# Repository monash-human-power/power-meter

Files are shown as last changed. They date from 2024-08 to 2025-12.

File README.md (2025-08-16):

# Cycling power meter final year project <!-- omit in toc -->
Oscar Varney and Jotham Gates, 2024

This is the code repository for a Final Year Project (FYP) to develop a crankset and power meter for Human Powered Vehicles (HPVs).

<p align="center">
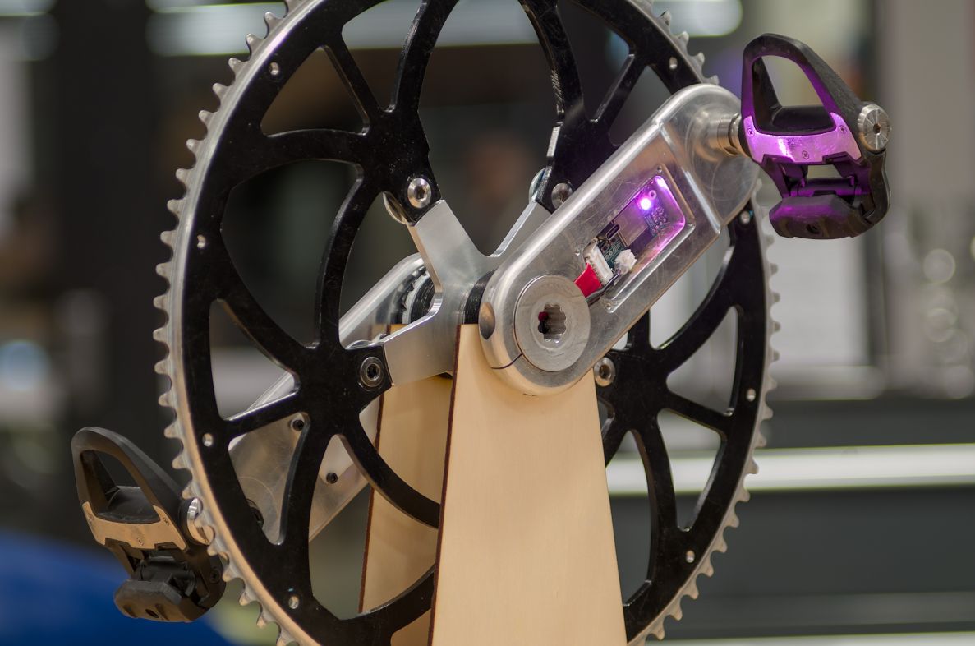
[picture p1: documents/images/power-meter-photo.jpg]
Pretty photo of the prototype crankset and power meter
    
</p>

## Contents <!-- omit in toc -->
- [Getting started](#getting-started)
- [Schematic and PCB layout](#schematic-and-pcb-layout)
- [Code](#code)
  - [Libraries](#libraries)
  - [Tools for updating dates of changed files and versions](#tools-for-updating-dates-of-changed-files-and-versions)
    - [Git Hook for checking dates are correct before committing](#git-hook-for-checking-dates-are-correct-before-committing)
  - [Doxygen documentation](#doxygen-documentation)
- [Scripts and testing](#scripts-and-testing)

## Getting started
- See [here](./documents/getting_started_mqtt.md) for some instructions on getting the power meter to work with MQTT and WiFi.
- See [here](./configs/README.md) for information on configuring the power meter.
- See [here](./documents/mqtt_topics.md) for information on MQTT topics used when communicating using this protocol.
- If you are a member of MHP, then the Notion page for this project can be found [here](https://www.notion.so/monashhumanpower/Power-Pedals-Cranks-FYP-3e6eb409a05642b1ad961b32c2f40aa7).
- The reports submitted for the project are [here](https://github.com/monash-human-power/power-meter-docs/releases) (private repository).

## Schematic and PCB layout
The schematic and PCB layout were completed using [KiCAD 9](https://www.kicad.org/). The design files are in the [`power-meter-pcb`](./power-meter-pcb/) folder.

## Code
The firmware is written to use the Arduino environment of Platform IO and is located in the [`power-meter-code`](power-meter-code) directory.

### Libraries
Install the following libraries, either by using the Arduino library manager or going to their GitHub repository and cloning them.
- [ArduinoJson](https://arduinojson.org/) library for JSON encoding and decoding.
- [ICM42670P](https://github.com/tdk-invn-oss/motion.arduino.ICM42670P) library for communicating with the IMU.
- [BasicLinearAlgebra](https://github.com/tomstewart89/BasicLinearAlgebra/) library for matrix maths. This is also added as a submodule for testing the Kalman filter on a computer.
- [ArduinoBLE](https://github.com/arduino-libraries/ArduinoBLE) library for Bluetooth Low Energy (BLE) communications.
- [PubSubClient](https://pubsubclient.knolleary.net/) library for communicating using MQTT over WiFi.

### Tools for updating dates of changed files and versions
A bash script has been written to update the dates on all modified or staged files (not including untracked files). To perform this operation, run:
```bash
./tools/update_date.sh
```

Another script is included to update the version info on all files and definitions for the code. The files and elements updated include:
- Any `@version` tags in the code directory.
- The `VERSION` definition in [`defines.h`](./power-meter-code/defines.h).
- The Doxygen version number in [`Doxyfile`](./Doxyfile).

As an example:
```bash
./tools/update_version.sh 1.2.3
```

#### Git Hook for checking dates are correct before committing
> This needs to be modified to work with the platform IO structure.
Copy the [`pre-commit`](./tools/pre-commit) file into [`.git/hooks/pre-commit`](.git/hooks/pre-commit). This will check the date of code files and make sure they are up to date.

### Doxygen documentation
Documentation can be automatically generated using Doxygen by running `doxygen` from the root folder of the repository. You might need to install doxygen and graphviz first. The output will be placed in the [`docs`](docs) folder. GitHub actions may be set up later down the track to automatically generate and deploy to GitHub pages on commit- however that would require a public repository and documentation.

To generate a massive appendix for the report, run `./tools/generate_refman.sh`

The output file will be [`refman.pdf`](docs/latex/refman.pdf).

## Scripts and testing
Scripts for testing the board hardware and easing development of certain sections can be found in the [`scripts-testing`](./scripts-testing/) directory. This includes python scripts used to log data over MQTT and plot it.

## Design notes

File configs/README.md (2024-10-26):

# Config files <!-- omit in toc -->
These JSON files contain calibration data and settings for the power meters.

- [Config format](#config-format)
  - [Example](#example)
  - [Key value pairs](#key-value-pairs)
  - [Notes](#notes)
    - [(1) More on Kalman filters](#1-more-on-kalman-filters)
    - [(2) Matrix representation](#2-matrix-representation)
    - [(3) Converting ADC values to torque](#3-converting-adc-values-to-torque)
- [Obtaining the current config from the device](#obtaining-the-current-config-from-the-device)
  - [Over MQTT](#over-mqtt)
  - [Through serial](#through-serial)
- [Uploading new configs to the device](#uploading-new-configs-to-the-device)
  - [Uploading over MQTT](#uploading-over-mqtt)
  - [Uploading over serial](#uploading-over-serial)

## Config format
The data is formatted into key-value pairs using JSON.

### Example
```json
{
    "connection": 0,
    "kalman": {
        "Q": [
            [2e-3, 0],
            [0, 0.1]
        ],
        "R": [
            [100, 0],
            [0, 1e-2]
        ]
    },
    "imuHowOften": 1,
    "sleep-time": 0,
    "left-strain": {
        "offset": 0,
        "coef": -3.679656e-4,
        "temp-test": 24.25,
        "temp-coef": 0
    },
    "right-strain": {
        "offset": 0,
        "coef": 2.246571e-4,
        "temp-test": 24.25,
        "temp-coef": 0
    },
    "mqtt": {
        "length": 20,
        "broker": "mhp-chase-car.local"
    },
    "wifi": {
        "ssid": "",
        "psk": "",
        "redacted": true
    }
}
```

### Key value pairs
| Key | Data type | Description | When changes are applied |
| :---: | :---: | :--- | :--- |
| `"connection"` | [`EnumSide`](../power-meter-code/src/defines.h#EnumSide)  | What connection method to use. `0` is MQTT and WiFi, `1` is Bluetooth Low Energy (BLE). Pressing the boot button after the power meter has started will also toggle this option and restart the power meter to apply it. | On boot |
| `"kalman"` | JSON object | Configurration values for the Kalman filter used to process data from the IMU. See [(1)](#1-more-on-kalman-filters) for more info. | |
| `"kalman"` - `"Q"` | $2 \times 2$ matrix (see [(2)](#2-matrix-representation)) | The covariance matrix representing environmental uncertainty. This increases the uncertainty of the historical predictions over time. Without going into details, increasing the top left number will make the system more uncertain about the previously predicted position, whilst increasing the bottom right number will make it more uncertain about the previously predicted velocity. | Instantly |
| `"kalman"` - `"R"` | $2 \times 2$ matrix (see [(2)](#2-matrix-representation)) | The covariance matrix representing measurement uncertainty. This represents the uncertainty of the most recent measurements from the IMU, making the filter rely more on predictions based off historical data. Without going into details, increasing the top left number will make the system more uncertain about the position measured by the accelerometer, whilst increasing the bottom right number will make it more uncertain about the measured velocity. | Instantly |
| `"imuHowOften"` | Integer | How often to save and transmit data from the IMU. `1` is every time. | Instantly |
| `"sleep-time"` | Integer | The number of seconds after the last forwards rotation occurred to go into sleep mode to save power. Setting this to 0 disables sleep mode entirely. For safety reasons / reducing the pain to unbrick if set to too short a value, this value will not be updated if it is between 0 and 20 seconds (inclusive). | Instantly |
| `"left-strain"` `"right-strain"` | JSON object | Calibration data for the strain gauges on each side. See [(3)](#3-converting-adc-values-to-torque) for more information on how these values are used to calculate torque. | |
| `"*-strain"` - `"offset"` | Unsigned 24 bit integer | Reading from the ADC when there is no torque applied. This is the 0 value. | Instantly |
| `"*-strain"` - `"coef"` | float | This is the coeficient used to scale the ADC reading to obtain the torque in Nm from the raw ADC reading. It needs to have the correct sign depending on the wheatstone bridge wiring and side of the meter. | Instantly |
| `"*-strain"` - `"temp-test"` | float | The temperature at which calibration occurred on that side. |
| `"*-strain"` - `"temp-coef"` | float | The temperature coefficient. | Instantly |

### Notes
#### (1) More on Kalman filters
[This](https://www.bzarg.com/p/how-a-kalman-filter-works-in-pictures/) is a really useful website that nicely describes with pictures how a multidimensional Kalman filter works and can be implemented.

The main aims / reasoning of using a Kalman filter are:
- The accelerometer's angle / measurement of the direction of gravity is stable over long periods of time. It is unreliable over short periods due to factors like rocks, vibration and falling off a cliff.
- The gyroscope is highly accurate at measuring instantaneous angular velocity. Finding position from this requires integration, which accrues error and drift over time.
- The filter combines the short term accuracy of the gyroscope with long term stability of the accelerometer to produce a nice, relatively noise free output of angular position and angular velocity.
- 
#### (2) Matrix representation
$2 \times 2$ matrices like the one shown below are represented using 2 dimensional arrays (same way as in numpy).
$$
A = \left[\begin{matrix} a & b \\ c & d\end{matrix}\right]
$$
Will be translated to:
```json
{
    "A": [[a, b], [c, d]]
}
```

#### (3) Converting ADC values to torque
The current formula is:

$$
\tau (x, t) = S_c \times (x - S_o) \times (1 - T_c) \times (t - T_o)
$$

##### Where <!-- omit in toc -->
- $\tau(x, t)$ is the calculated torque, $\tau$ for a given ADC reading, $x$ and temperature in Celcius, $t$.
- $S_c$ is the coefficient for the strain gauges and ADC (`"coef"`).
- $S_o$ is the offset (what the ADC resports when no torque is applied, `"offset"`).
- $T_c$ is the temperature coefficient (set to 0 to disable temperature compensation, `"temp-coef"`).
- $T_o$ is the temperature offset (temperature that the calibration to measure $S_c$ took place, `"temp-test"`).

## Obtaining the current config from the device
### Over MQTT
The config is published as part of a message on the [`/power/about`](../documents/mqtt_topics.md#about-this-device-powerabout) topic when the power meter connects to the broker.

### Through serial
1. Connect a USB cable and open a serial terminal.
2. Press `g` to print out the current config stored on the device. Make changes as necessary.
3. Typing `h` lists other potentially useful commands.

## Uploading new configs to the device
### Uploading over MQTT
These can be uploaded over MQTT using:
```
mosquitto_pub -t "/power/conf" -f FirstPrototype_130.json
```

### Uploading over serial
They can also be uploaded over the serial port:
1. Connect a USB cable and open a serial terminal.
2. Press `g` to print out the current config stored on the device. Make changes as necessary.
3. Press `s` to set the config. Remove all new lines and paste the json document. Press enter if needed afterwards to apply. There is a 30 second time limit.
4. Confirm that the config is successfully set.

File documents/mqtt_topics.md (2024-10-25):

# MQTT Topics <!-- omit in toc -->
When running in WiFi and MQTT mode, the power meter publishes data to several topics. All topics are prefixed by `/power/` to distinguish data sent to and from the power meter with other traffic on the broker.

- [Published topics](#published-topics)
  - [About this device (`/power/about`)](#about-this-device-powerabout)
    - [Example](#example)
    - [Key value pairs](#key-value-pairs)
  - [Housekeeping data (`/power/housekeeping`)](#housekeeping-data-powerhousekeeping)
    - [Example](#example-1)
    - [Key value pairs](#key-value-pairs-1)
  - [Slow speed data (`/power/power`)](#slow-speed-data-powerpower)
    - [Example](#example-2)
    - [Key value pairs](#key-value-pairs-2)
  - [High speed IMU data (`/power/imu`)](#high-speed-imu-data-powerimu)
    - [Record format](#record-format)
  - [High speed strain gauge data (`/power/fast/left`, `/power/fast/right`)](#high-speed-strain-gauge-data-powerfastleft-powerfastright)
    - [Record format](#record-format-1)
- [Subscribed topics](#subscribed-topics)
  - [Set a new configurration (`/power/conf`)](#set-a-new-configurration-powerconf)
  - [Calculate and apply new offsets on the strain gauge ADCs (`/power/offset`)](#calculate-and-apply-new-offsets-on-the-strain-gauge-adcs-poweroffset)
    - [Example usage](#example-usage)
  - [Save configs (`/power/save`)](#save-configs-powersave)
  - [Reboot (`/power/reboot`)](#reboot-powerreboot)
  - [Enter sleep mode (`/power/sleep`)](#enter-sleep-mode-powersleep)
- [Additional notes](#additional-notes)

## Published topics
These topics contain data from the power meter. Messages sent less frequently are formatted using JSON for easier reading and processing. Messages containing high frequency data (IMU and strain gauges) are packed into bytes.

### About this device (`/power/about`)
This message is sent whenever the power meter connects to the broker. It contains information relating to the software and hardware versions, as well as the current configurrations.

#### Example
An example message after pretty-printing is:
```json
{
    "name": "Power meter prototype",
    "compiled": "Sep 30 2024, 22:38:28",
    "sw_version": "s0.1.0",
    "hw_version": "v1.1.1",
    "connect-time": 7336,
    "calibration": {
        "connection": 0,
        "kalman": {
            "Q": [
                [2e-3, 0],
                [0, 0.1]
            ],
            "R": [
                [100, 0],
                [0, 1e-2]
            ]
        },
        "imuHowOften": 1,
        "sleep-time": 0,
        "left-strain": {
            "offset": 0,
            "coef": -3.679656e-4,
            "temp-test": 24.25,
            "temp-coef": 0
        },
        "right-strain": {
            "offset": 0,
            "coef": 2.246571e-4,
            "temp-test": 24.25,
            "temp-coef": 0
        },
        "mqtt": {
            "length": 20,
            "broker": "mhp-chase-car.local"
        },
        "wifi": {
            "ssid": "",
            "psk": "",
            "redacted": true
        }
    },
    "mac": "XX:XX:XX:XX:XX:XX"
}
```

#### Key value pairs
| Key | Data type | Description |
| :---: | :---: | :--- |
| `"name"` | string | The device name, set in [constants.h](../power-meter-code/src/constants.example.h). |
| `"compiled"` | string | The date and time that the firmware was compiled according to the computer that did the compiling. |
|  `"sw_version"`  | string | The firmware version (set in [defines.h](../power-meter-code/src/defines.h)). |
|  `"hw_version"`  | string | The targeted hardware version, set in [constants.h](../power-meter-code/src/constants.example.h). |
| `"connect-time"` | unsigned 32 bit integer | The number of microseconds since the microcontroller was reset. This rills over approximately every hour. |
| `"calibration"`  | JSON object | The current config value loaded into memory. See the [`/power/conf`](#set-a-new-configurration-powerconf) topic or [this page](../configs/README.md) for more details. |
| `"mac"` | string | The MAC address of the microcontroller in the power meter. This is aking to a serial number and is useful for identifying which power meter recorded the data. |

### Housekeeping data (`/power/housekeeping`)
This message is sent once every few seconds and contains information on the device health and environmental conditions. It is designed for information that updates faster than that sent in the [about message](#about-this-device-powerabout), but is not time critical like that sent in the power and high frequency messages.

#### Example
An example message after pretty-printing is:
```json
{
    "temps": {
        "left": 24.00,
        "right": -1000.00,
        "imu": 35.00
    },
    "battery": 3299.00,
    "left-offset": 9848390,
    "right-offset": 6252516
}
```

#### Key value pairs
| Key | Data type | Description |
| :---: | :---: | :--- |
| `"temps"` | JSON object | This field contains the temperatures for each side and that reported by the IMU. All values within this are floating point in Celcius. A value of `-1000.00` represents not being able to successfully communicate with the sensor. |
| `"battery"` | float | The battery voltage in mV. |
| `"left-offset"`, `"right-offset"` | unsigned 32 bit integer | The current offsets being used by each ADC. This value represents 0 torque on each side. |

### Slow speed data (`/power/power`)
This message contains information averaged over the last complete rotation. This message is sent every rotation or every few seconds, whichever comes sooner. Most of the useful data that the riders care about mid-ride will come from this message.

#### Example
An example message after pretty-printing is:
```json
{
    "timestamp": 311280713,
    "cadence": 70.1,
    "rotations": 185,
    "power": 390.6,
    "balance": 50.8
}
```

#### Key value pairs
| Key | Data type | Description |
| :---: | :---: | :--- |
| `"timestamp"` | unsigned 32 bit integer | The system time in microseconds when the last rotation occurred. |
|  `"cadence"`  | float | The average cadence over the last complete rotation in RPM. |
| `"rotations"` | unsigned 32 bit integer | The total number of rotations since the device was reset. |
| `"power"` | float | The power over the last rotation in W. If this message is being sent according to a schedule rather than a rotation completing, this will be 0. |
|  `"balance"`  | float | The pedal balance in percent. A value of 50% means that both sides are recording equal power. A value of 0% means that all power is being generated by one side and a value of 100% means all power is being generated by the other side. TODO: Work out which side is which. |

### High speed IMU data (`/power/imu`)
This message contains multiple records of the 100Hz sampled IMU data. Because a lot of this data needs to be sent over the network, structures of bytes are used rather than converting to ASCII and JSON formats.

Each message is comprised of many individual records. The oldest records are arranged at the start of the message, whilst the most recent are at the back. Each message will be a multiple of the size of each record's length. The number of records per message is set in the [configurration](../configs/README.md).
| Byte offset in record |        Data type        | Size in bytes | 

#### Record format
| Byte offset in record | Data type | Size in bytes | Description |
| :---: | :---: | :---: | :--- |
| 0 | unsigned 32 bit integer | 4 | The device time in microseconds when the sample was captured. |
| 4 | float | 4 | The angular velocity in radians per second of the power meter. This is an output from the on-board Kalman filter. |
| 8 | float | 4 | The position in radians of the power meter. This is an output from the on-board Kalman filter. |
| 12 | float | 4 | The acceleration in m/s^2 for the X axis. This has been corrected for centripedal forces caused by the IMU not being at the center of rotation of the power meter. |
| 16 | float | 4 | The acceleration in m/s^2 for the Y axis. This has been corrected for centripedal forces caused by the IMU not being at the center of rotation of the power meter. |
| 20 | float | 4 | The acceleration in m/s^2 for the Z axis. |
| 24 | float | 4 | The angular velocity of the X axis in radians per second as measured by the gyroscope. |
| 28 | float | 4 | The angular velocity of the Y axis in radians per second as measured by the gyroscope. |
| 32 | float | 4 | The angular velocity of the Z axis in radians per second as measured by the gyroscope. |

### High speed strain gauge data (`/power/fast/left`, `/power/fast/right`)
This message contains multiple records of the 80Hz sampled strain gauge data for a side. Because a lot of this data needs to be sent over the network, structures of bytes are used rather than converting to ASCII and JSON formats.

Each message is comprised of many individual records. The oldest records are arranged at the start of the message, whilst the most recent are at the back. Each message will be a multiple of the size of each record's length. The number of records per message is set in the [configurration](../configs/README.md).

#### Record format
| Byte offset in record | Data type | Size in bytes | Description |
| :---: | :---: | :---: | :--- |
| 0 | unsigned 32 bit integer | 4 | The device time in microseconds when the sample was captured. |
| 4 | float | 4 | The angular velocity in radians per second of the power meter. This is an output from the on-board Kalman filter that has been predicted at the current time. |
| 8 | float | 4 | The position in radians of the power meter. This is an output from the on-board Kalman filter that has been predicted at the current time. |
| 12 | unsigned 24 bit integer | 4 | The raw reading from the ADC. Whilst the output from the ADCs is a 24 bit number, the value is being sent as an unsigned 32 bit integer to simplify processing. |
| 16 | float | 4 | The calculated torque in Nm. |
| 20 | float | 4 | The calculate power in W. This is the torque multiplied by the angular velocity. |
| 24 | bool | 1 | Whether the device was transmitting when the sample was taken. This might be useful for noise filtering as the power supply on the microcontroller side is affected. |

## Subscribed topics
### Set a new configurration (`/power/conf`)
See [here](../configs/README.md) for more information on the message format and alternative ways to set configs.

### Calculate and apply new offsets on the strain gauge ADCs (`/power/offset`)
Messages sent to this topic will cause the device to take many samples from the ADC, average them and use them as the offset from now on. These offsets are not stored in flash memory and will be restored to the defaults or those loaded into flash memory upon reboot.

#### Example usage
```bash
mosquitto_pub -t "/power/offset" -m ""
```

### Save configs (`/power/save`)
*Not implemented yet.*

### Reboot (`/power/reboot`)
This would be useful to load new configs / start from a defined base.
*Not implemented yet.*

### Enter sleep mode (`/power/sleep`)
This would be useful to shut the system down and save power manually. It would also be useful to cleanly disconnect from the current connection so that the router / device managing the connection doesn't throw a wobbly if power is removed and reapplied with no warning.

*Not implemented yet.*

## Additional notes
- Integers are sent using little endian.
- Floats are single precision for improved processing performance. They are stored and sent in the IEEE 754 binary32 format (native on the ESP32 and most computers).

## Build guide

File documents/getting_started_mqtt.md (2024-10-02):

# Getting started (connecting over WiFi and MQTT) <!-- omit in toc -->

- [What you will need](#what-you-will-need)
- [Setting up to log and display data](#setting-up-to-log-and-display-data)
- [Turning the power meter on](#turning-the-power-meter-on)

## What you will need
- A WiFi network / mobile phone hotspot (2.4GHz) that the power meter is configurred to connect to (see [configurations](../configs/README.md)).
- An MQTT broker that the power meter is configurred to connect to (see [configurations](../configs/README.md)).
- A computer with:
  - A copy of this repository cloned to it.
  - [Python3](https://www.python.org/) installed.
  - The MQTT broker and WiFi network may be running or hosted on this computer (optional).

## Setting up to log and display data
1. Open a terminal and change the working directory to the [repository root](../).
2. **Optional:** Create a python virtual environment to keep the packages installed in this project separate from the rest of the system.
    ```bash
    # Linux
    pip3 -m venv .venv

    # Windows
    pip -m venv venv
    ```
3. Activate the virtual environment if using it.
    ```bash
    # Linux
    source .venv/bin/activate

    # Windows
    # See 
    venv\Scripts\Activate.ps1
    ```
    You will notive that each line in the terminal now starts with `(.venv)`.
4. Install the required packages:
    ```bash
    pip3 install -r requirements.txt
    ```
5. Change directory to the [`scripts-testing/python-clients`](../scripts-testing/python-clients/) folder.
6. Run the [logging script](../scripts-testing/python-clients/log_power_meter.py):
    ```bash
    ./log_power_meter.py
    ```
    By default, this will attempt to subscribe to a broker running on the same computer the script is being run from. Pass `-h HOST_OR_IP` to change this. To see other options available, run the script with `--help`.
7. It may be worthwhile opening another terminal to subscribe to the low speed topics to display messages as they arrive with:
    ```bash
    mosquitto_sub -t "/power/about" -t "/power/power" -t "/power/housekeeping" -v
    ```
    Again use `-h HOST_OR_IP` to specify an alternate MQTT broker if needed.
8. Use `Ctrl` + `C` to close both of these programmes.

## Turning the power meter on
1. Install the battery and plug it into the board. Make sure the end cap on the axle is done up sufficiently to stop the crank arm falling off.
2. The V1.1.1 power meters will flash the yellow LEDs on each side followed by a blue flash on the RGB LED when they are trying to connect to WiFi. Make sure that the yellow LEDs on both sides are flashing (sometimes power needs to be removed and re-applied to get the temperature sensors they are connected to, to initialise correctly).
3. If the power meter is stuck in this connecting to WiFi state, make sure that the WiFi network is running with the same SSID and password as the power meter is configured to connect to. Make sure that it uses 2.4GHz WiFi as the built in microcontroller does not support the 5GHz band. If none of these work, use a [USB cable to check and update the configs on the device as needed](../configs/README.md#through-serial).
4. Once connected to WiFi, the yellow LEDs on each side will continue to flash and the RGB LED will flash green. In this state, the device is trying to connect to the broker. If this does not happen successfully, make sure the broker is configurred correctly and the broker is running and reachable from other computers.
5. The RGB LED will flicker green when the power meter is connected and sending data.
6. To manually measure and apply offsets, publish a message to the `/power/offset` topic using the following command:
    ```bash
    mosquitto_pub -t "/power/offset" -m ""
    ```

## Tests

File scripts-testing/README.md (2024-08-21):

# Testing scripts and development
## Logging data to a file and plotting it.
The python scripts in the [`python-clients`](./python-clients/) directory allow data to be saved, unpacked into human-readable form and saved as needed.
- [`log_power_meter.py`](./python-clients/log_power_meter.py) logs data to a folder of files or displays it live.
- [`plot_imu_timeseries.py`](./python-clients/plot_imu_timeseries.py) plots IMU data.

## Board testing
These scripts help to verify that the hardware is working correctly. It is recommended to run these scripts in the following order. The next one usually depends on the previous working.

### 1. [LED testing](./led-testing/)
This script turns on and flashes the red and green LEDs (D1 and D2).

### 2. [Accelerometer polling](./accel-testing/)
> Relies on [LED testing](#1-led-testing) passing.

This script regularly polls the IMU and sets the colour of the LEDs based on the readings of the X axis accelerometer (tilt to change colour). The values read are also sent over the serial port.

This script is based off the [ICM42670P Arduino library `Polling_SPI`](https://github.com/tdk-invn-oss/motion.arduino.ICM42670P/blob/main/examples/Polling_SPI/Polling_SPI.ino) example.

### 3. [Accelerometer interrupts](./accel_testing-fifo/)
> Relies on [LED testing](#1-led-testing) and [Accelerometer polling](#2-accelerometer-polling) passing.

This script behaves the same as the polling script, however it uses the FIFO buffer and interrupts to obtain the data.

This script is based off the [ICM42670P Arduino library `FIFO_Interrupt`](https://github.com/tdk-invn-oss/motion.arduino.ICM42670P/blob/main/examples/FIFO_Interrupt/FIFO_Interrupt.ino) example.

### 4. [GPIO Testing for the ADC pins](./gpio-testing/)
> Relies on [LED testing](#1-led-testing) and USB / the ability to accept numbers from `Serial.parseInt()`.

This script toggles pins as given over the serial port. This can be used to check that they were soldered correctly and are not disconnected or shorted out.

Usage instructions:
- Red light indicates waiting for a pin number to be typed in the serial console.
- Flashing green indicates that a pin is being tested (on is high, off is low).
- Press 'q' to got back and select another pin.
- All pins other than LEDs are left in high impedance states after testing that pin concludes.

### 5. Temperature sensor and LED testing
> Relies on [LED testing](#1-led-testing) for pretty lights and a serial connection to show temperatures.

This script reads the temperatures on both I2C sensors and flashes the temperature sensor and built in LEDs.

## Kalman filter development
[`kalman-compare.py`](./kalman-filter/kalman-compare.py) takes a CSV file from the power meter and plots the reported orientation over time. This script also calculates orientation based on the accelerometer alone, gyroscope alone and a python implementation of the Kalman filter to compare the results.

The [`AccelGyroData.ipynb`](./kalman-filter/AccelGyroData.ipynb) Jupyter notebook contains initial code used to test the Kalman filter algorithm with data recorded from a phone taped to a bicycle crank prior to the actual hardware being available. The data was recorded using the [Sensor Logger app](https://play.google.com/store/apps/details?id=com.kelvin.sensorapp&hl=en_US).

[`kalman_test.cpp`](./kalman-filter/kalman_test.cpp) tests the actual Kalman filter implementation whilst running on a computer. Compile this programme using `make kalman` and run it using `make run`.

The [BasicLinearAlgebra](https://github.com/tomstewart89/BasicLinearAlgebra/) library is included as a submodule to assist.

## Python libraries and environments
The [`requirements.txt`](../requirements.txt) file in the root of the repository contains all necessary libraries for all python scripts and Jupyter notebooks in this repository. As usual, it is recommended to use a python virtual environment. This can be created and the libraries installed (running from the repository-root directory) using:
```bash
python3 -v venv .venv
source .venv/bin/activate
pip3 -r requirements.txt
```

To save / update [`requirements.txt`](../requirements.txt), run [`./tools/update_requirements.sh`](../tools/update_requirements.sh) or run:
```bash
source .venv/bin/activate
pip3 freeze > requirements.txt
```

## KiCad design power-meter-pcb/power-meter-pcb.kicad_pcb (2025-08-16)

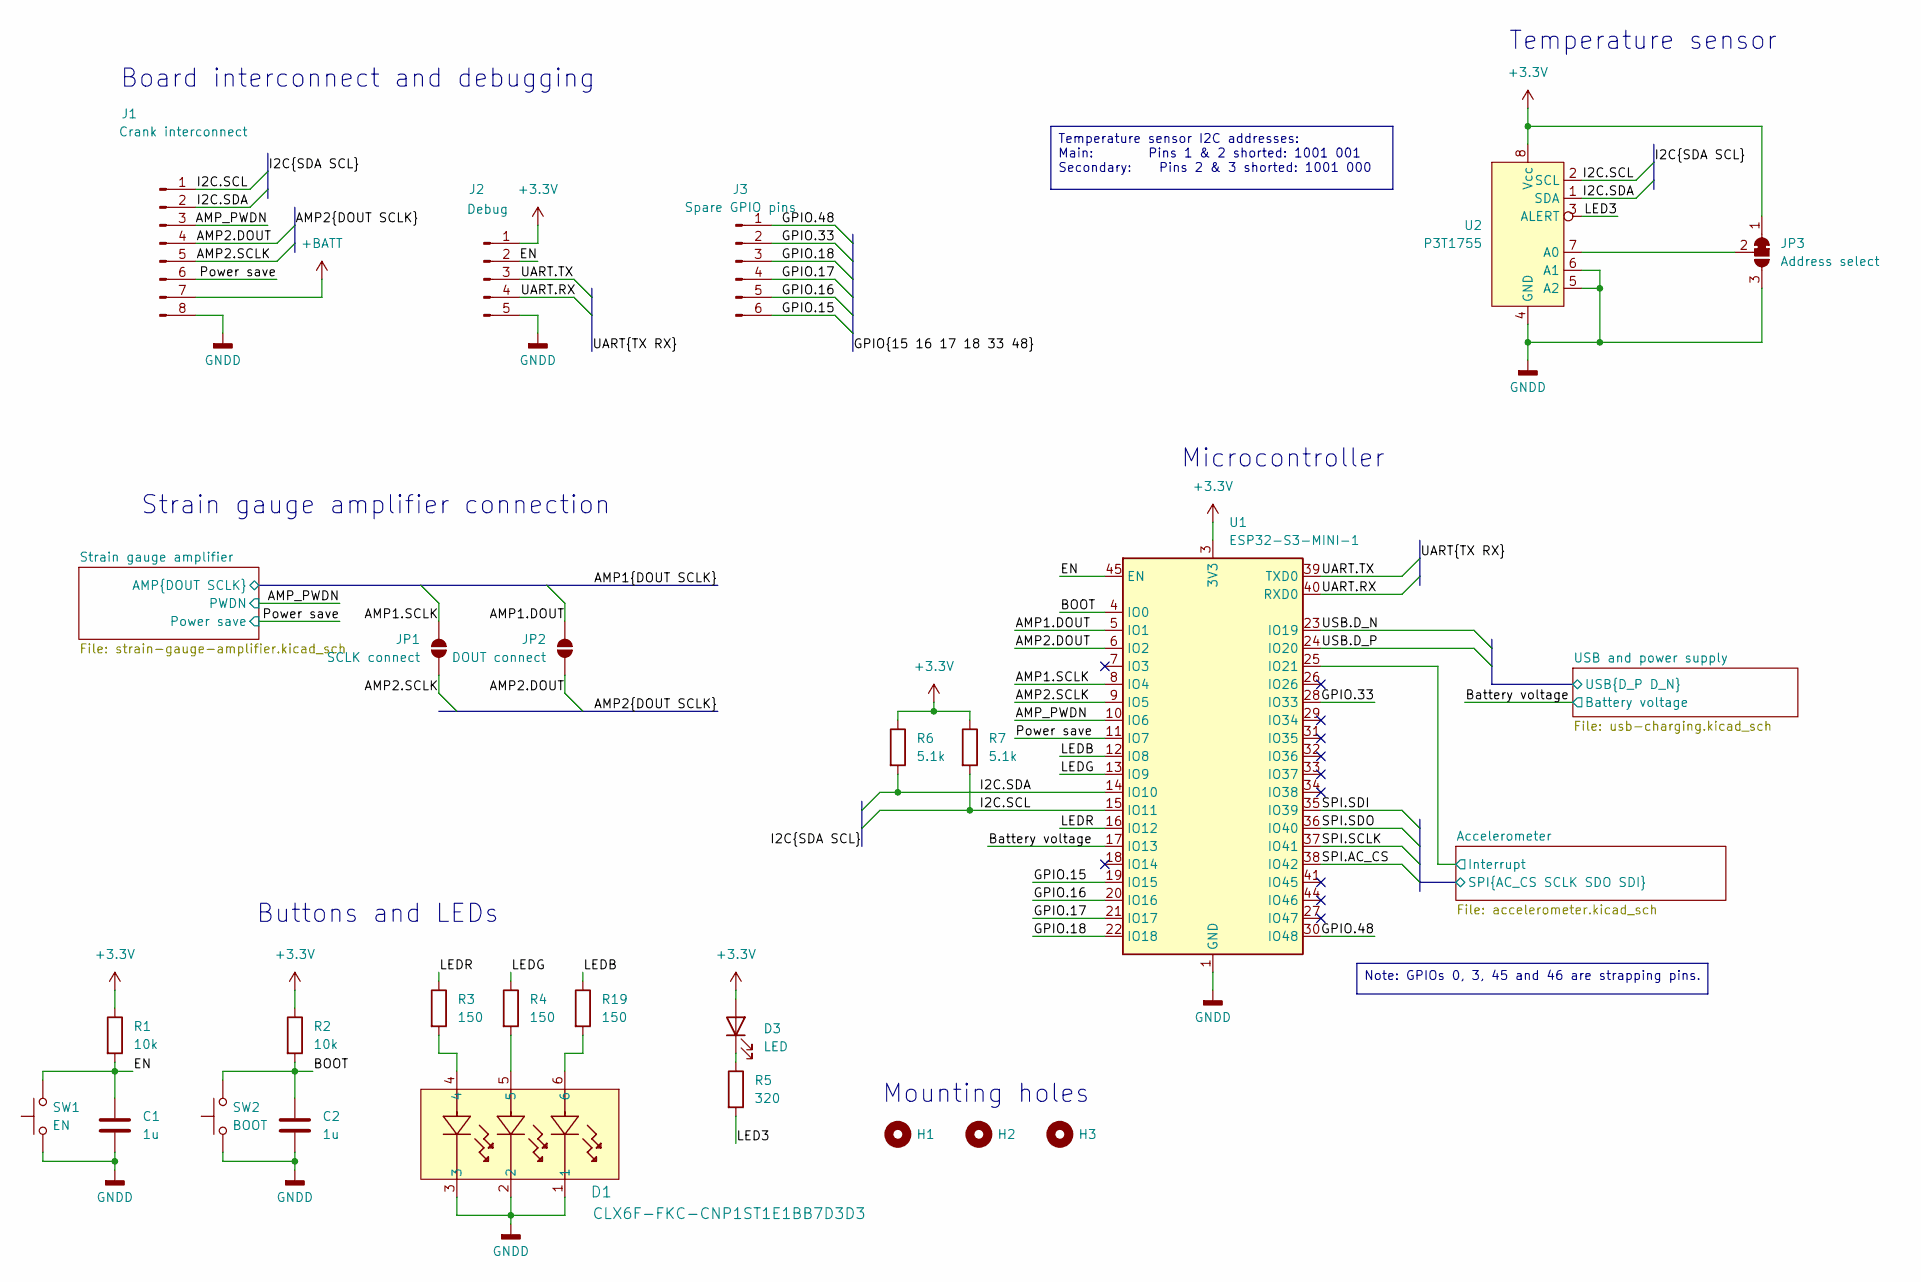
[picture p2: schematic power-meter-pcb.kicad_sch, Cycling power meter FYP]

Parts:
C1, C2: 1u; C_0603_1608Metric_Pad1.08x0.95mm_HandSolder
D1: CLX6F-FKC-CNP1ST1E1BB7D3D3; PLCC6_3.4X3.4_CRW-M
D3: LED; LED_0603_1608Metric_Pad1.05x0.95mm_HandSolder
H1, H2, H3: MountingHole; MountingHole_2.2mm_M2
J1: Crank interconnect; JST_PH_S8B-PH-K_1x08_P2.00mm_Horizontal
J2: Debug; PinHeader_1x05_P2.54mm_Vertical
J3: Spare GPIO pins; PinHeader_1x06_P2.00mm_Vertical
JP1: SCLK connect; SolderJumper-2_P1.3mm_Open_RoundedPad1.0x1.5mm
JP2: DOUT connect; SolderJumper-2_P1.3mm_Open_RoundedPad1.0x1.5mm
JP3: Address select; SolderJumper-3_P1.3mm_Open_RoundedPad1.0x1.5mm
R1, R2: 10k; R_0603_1608Metric_Pad0.98x0.95mm_HandSolder
R3, R4, R19: 150; R_0603_1608Metric_Pad0.98x0.95mm_HandSolder
R5: 320; R_0603_1608Metric_Pad0.98x0.95mm_HandSolder
R6, R7: 5.1k; R_0603_1608Metric_Pad0.98x0.95mm_HandSolder
SW1: EN; SW_Push_1P1T_NO_CK_KMR2
SW2: BOOT; SW_Push_1P1T_NO_CK_KMR2
U1: ESP32-S3-MINI-1; ESP32-S2-MINI-1
U2: P3T1755; TSSOP-8_3x3mm_P0.65mm

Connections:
+3.3V: D3.2 (A), J2.1, JP3.1 (A), R1.1, R2.1, R6.1, R7.1, U1.3 (3V3), U2.8 (Vcc); also elsewhere on the board
+BATT: J1.7; also elsewhere on the board
/AMP1.DOUT: JP2.2 (B), U1.5 (IO1); also elsewhere on the board
/AMP1.SCLK: JP1.2 (B), U1.8 (IO4); also elsewhere on the board
/AMP2.DOUT: J1.4, JP2.1 (A), U1.6 (IO2)
/AMP2.SCLK: J1.5, JP1.1 (A), U1.9 (IO5)
/AMP_PWDN: J1.3, U1.10 (IO6); also elsewhere on the board
/Accelerometer/Interrupt: U1.25 (IO21); also elsewhere on the board
/Accelerometer/SPI.AC_CS: U1.38 (IO42); also elsewhere on the board
/Accelerometer/SPI.SCLK: U1.37 (IO41); also elsewhere on the board
/Accelerometer/SPI.SDI: U1.35 (IO39); also elsewhere on the board
/Accelerometer/SPI.SDO: U1.36 (IO40); also elsewhere on the board
/BOOT: C2.2, R2.2, SW2.2, U1.4 (IO0)
/Battery voltage: U1.17 (IO13); also elsewhere on the board
/EN: C1.2, J2.2, R1.2, SW1.2, U1.45 (EN)
/GPIO.15: J3.6, U1.19 (IO15)
/GPIO.16: J3.5, U1.20 (IO16)
/GPIO.17: J3.4, U1.21 (IO17)
/GPIO.18: J3.3, U1.22 (IO18)
/GPIO.33: J3.2, U1.28 (IO33)
/GPIO.48: J3.1, U1.30 (IO48)
/I2C.SCL: J1.1, R7.2, U1.15 (IO11), U2.2 (SCL)
/I2C.SDA: J1.2, R6.2, U1.14 (IO10), U2.1 (SDA)
/LED3: R5.2, U2.3 (ALERT)
/LEDB: R19.1, U1.12 (IO8)
/LEDG: R4.1, U1.13 (IO9)
/LEDR: R3.1, U1.16 (IO12)
/Power save: J1.6, U1.11 (IO7); also elsewhere on the board
/UART.RX: J2.4, U1.40 (RXD0)
/UART.TX: J2.3, U1.39 (TXD0)
/USB and power supply/USB.D_N: U1.23 (IO19); also elsewhere on the board
/USB and power supply/USB.D_P: U1.24 (IO20); also elsewhere on the board
GNDD: C1.1, C2.1, D1.1, D1.2, D1.3, J1.8, J2.5, JP3.3 (B), SW1.1, SW2.1, U1.1 (GND), U1.2 (GND), U1.42 (GND), U1.43 (GND), U1.46 (GND), U1.47 (GND), U1.48 (GND), U1.49 (GND), U1.50 (GND), U1.51 (GND), U1.52 (GND), U1.53 (GND), U1.54 (GND), U1.55 (GND), U1.56 (GND), U1.57 (GND), U1.58 (GND), U1.59 (GND), U1.60 (GND), U1.61 (GND), U1.62 (GND), U1.63 (GND), U1.64 (GND), U1.65 (GND), U2.4 (GND), U2.5 (A2), U2.6 (A1); also elsewhere on the board
unnamed: D1.4, R3.2
unnamed: D1.5, R4.2
unnamed: D1.6, R19.2
unnamed: D3.1 (K), R5.1
unnamed: JP3.2 (C), U2.7 (A0)

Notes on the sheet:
Board interconnect and debugging
Buttons and LEDs
Strain gauge amplifier connection
Microcontroller
Mounting holes
Temperature sensor
Note: GPIOs 0, 3, 45 and 46 are strapping pins.
Temperature sensor I2C addresses: Main: Pins 1 & 2 shorted: 1001 001 Secondary: Pins 2 & 3 shorted: 1001 000

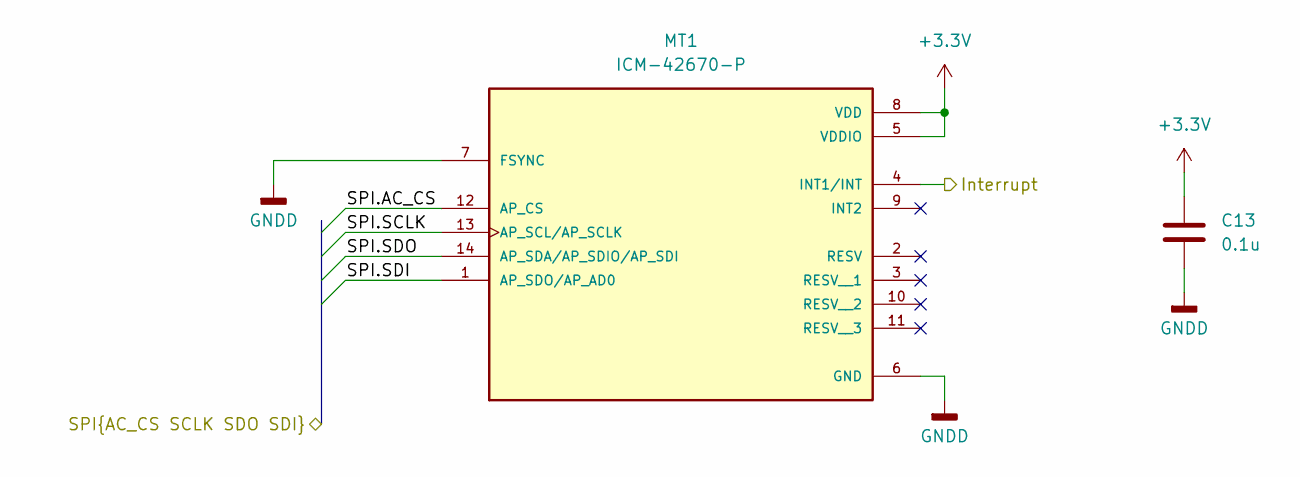
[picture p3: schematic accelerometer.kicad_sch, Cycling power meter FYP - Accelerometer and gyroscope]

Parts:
C13: 0.1u; C_0603_1608Metric_Pad1.08x0.95mm_HandSolder
MT1: ICM-42670-P; XDCR_ICM-42670-P; PARTREV 1.1

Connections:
+3.3V: C13.1, MT1.5 (VDDIO), MT1.8 (VDD); also elsewhere on the board
/Accelerometer/Interrupt: MT1.4 (INT1/INT); also elsewhere on the board
/Accelerometer/SPI.AC_CS: MT1.12 (AP_CS); also elsewhere on the board
/Accelerometer/SPI.SCLK: MT1.13 (AP_SCL/AP_SCLK); also elsewhere on the board
/Accelerometer/SPI.SDI: MT1.1 (AP_SDO/AP_AD0); also elsewhere on the board
/Accelerometer/SPI.SDO: MT1.14 (AP_SDA/AP_SDIO/AP_SDI); also elsewhere on the board
GNDD: C13.2, MT1.6 (GND), MT1.7 (FSYNC); also elsewhere on the board

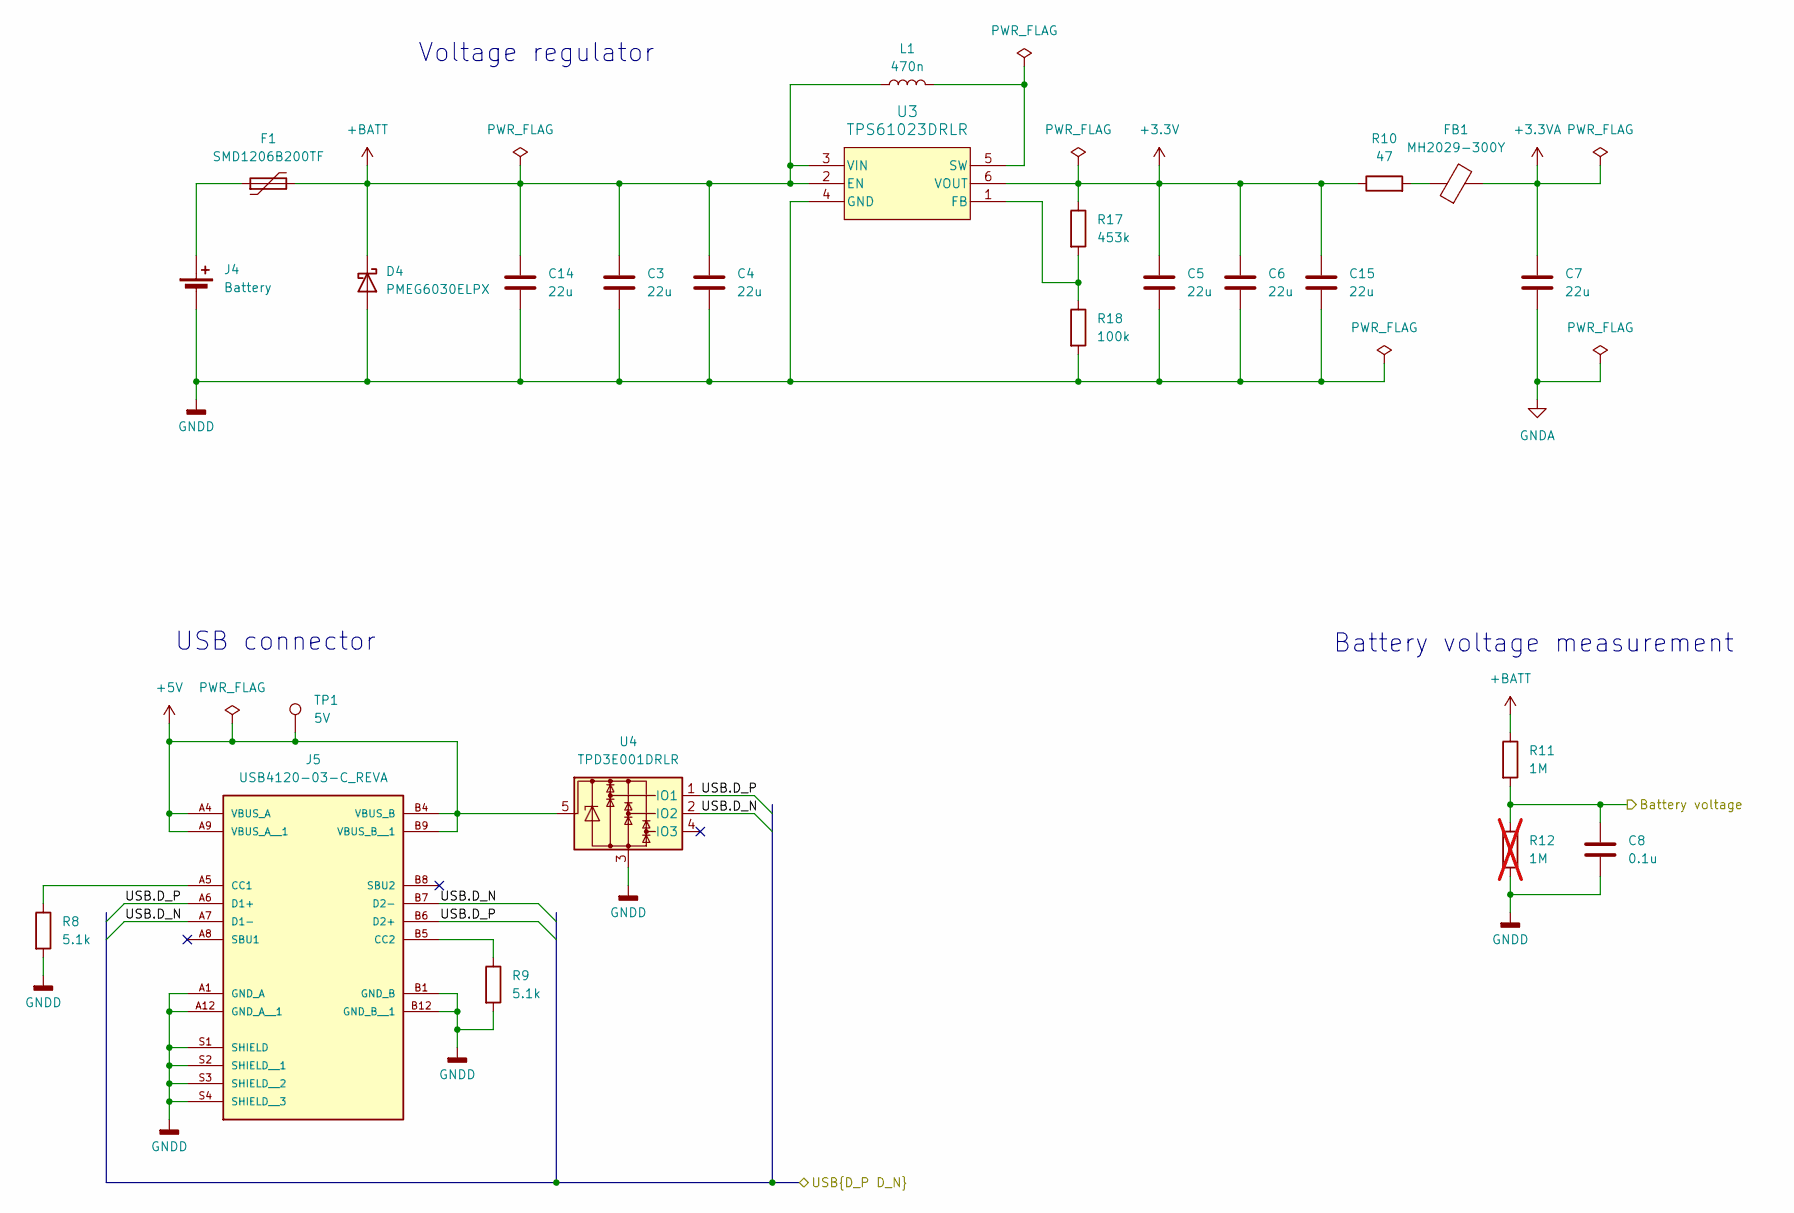
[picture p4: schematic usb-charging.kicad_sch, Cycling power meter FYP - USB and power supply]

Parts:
C3, C4, C5, C6, C7, C14, C15: 22u; C_0603_1608Metric_Pad1.08x0.95mm_HandSolder
C8: 0.1u; C_0603_1608Metric_Pad1.08x0.95mm_HandSolder
D4: PMEG6030ELPX; D_SOD-128
F1: SMD1206B200TF; Fuse_1206_3216Metric_Pad1.42x1.75mm_HandSolder
FB1: MH2029-300Y; L_0805_2012Metric
J4: Battery; JST_PH_S2B-PH-K_1x02_P2.00mm_Horizontal
J5: USB4120-03-C_REVA; GCT_USB4120-03-C_REVA; PARTREV A
L1: 470n; L_Vishay_IHLP-1212
R8, R9: 5.1k; R_0603_1608Metric_Pad0.98x0.95mm_HandSolder
R10: 47; R_0603_1608Metric_Pad0.98x0.95mm_HandSolder
R11: 1M; R_0603_1608Metric_Pad0.98x0.95mm_HandSolder
R12: 1M; R_0603_1608Metric_Pad0.98x0.95mm_HandSolder; not fitted
R17: 453k; R_0603_1608Metric_Pad0.98x0.95mm_HandSolder
R18: 100k; R_0603_1608Metric_Pad0.98x0.95mm_HandSolder
TP1: 5V; TestPoint_Pad_1.5x1.5mm
U3: TPS61023DRLR; DRL0006A
U4: TPD3E001DRLR; SOT-553

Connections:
+3.3V: C5.1, C6.1, C15.1, R10.1, R17.1, U3.6 (VOUT); also elsewhere on the board
+3.3VA: C7.1, FB1.2; also elsewhere on the board
+5V: J5.A4 (VBUS_A), J5.A9 (VBUS_A__1), J5.B4 (VBUS_B), J5.B9 (VBUS_B__1), TP1.1, U4.5
+BATT: C3.1, C4.1, C14.1, D4.1 (K), F1.2, L1.1, R11.1, U3.2 (EN), U3.3 (VIN); also elsewhere on the board
/Battery voltage: C8.1, R11.2, R12.1; also elsewhere on the board
/USB and power supply/USB.D_N: J5.A7 (D1-), J5.B7 (D2-), U4.2 (IO2); also elsewhere on the board
/USB and power supply/USB.D_P: J5.A6 (D1+), J5.B6 (D2+), U4.1 (IO1); also elsewhere on the board
GNDA: C7.2; also elsewhere on the board
GNDD: C3.2, C4.2, C5.2, C6.2, C8.2, C14.2, C15.2, D4.2 (A), J4.2 (-), J5.A1 (GND_A), J5.A12 (GND_A__1), J5.B1 (GND_B), J5.B12 (GND_B__1), J5.S1 (SHIELD), J5.S2 (SHIELD__1), J5.S3 (SHIELD__2), J5.S4 (SHIELD__3), R8.2, R9.2, R12.2, R18.2, U3.4 (GND), U4.3; also elsewhere on the board
unnamed: FB1.1, R10.2
unnamed: F1.1, J4.1 (+)
unnamed: J5.A5 (CC1), R8.1
unnamed: J5.B5 (CC2), R9.1
unnamed: R17.2, R18.1, U3.1 (FB)
unnamed: L1.2, U3.5 (SW)

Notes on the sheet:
Battery voltage measurement
USB connector
Voltage regulator

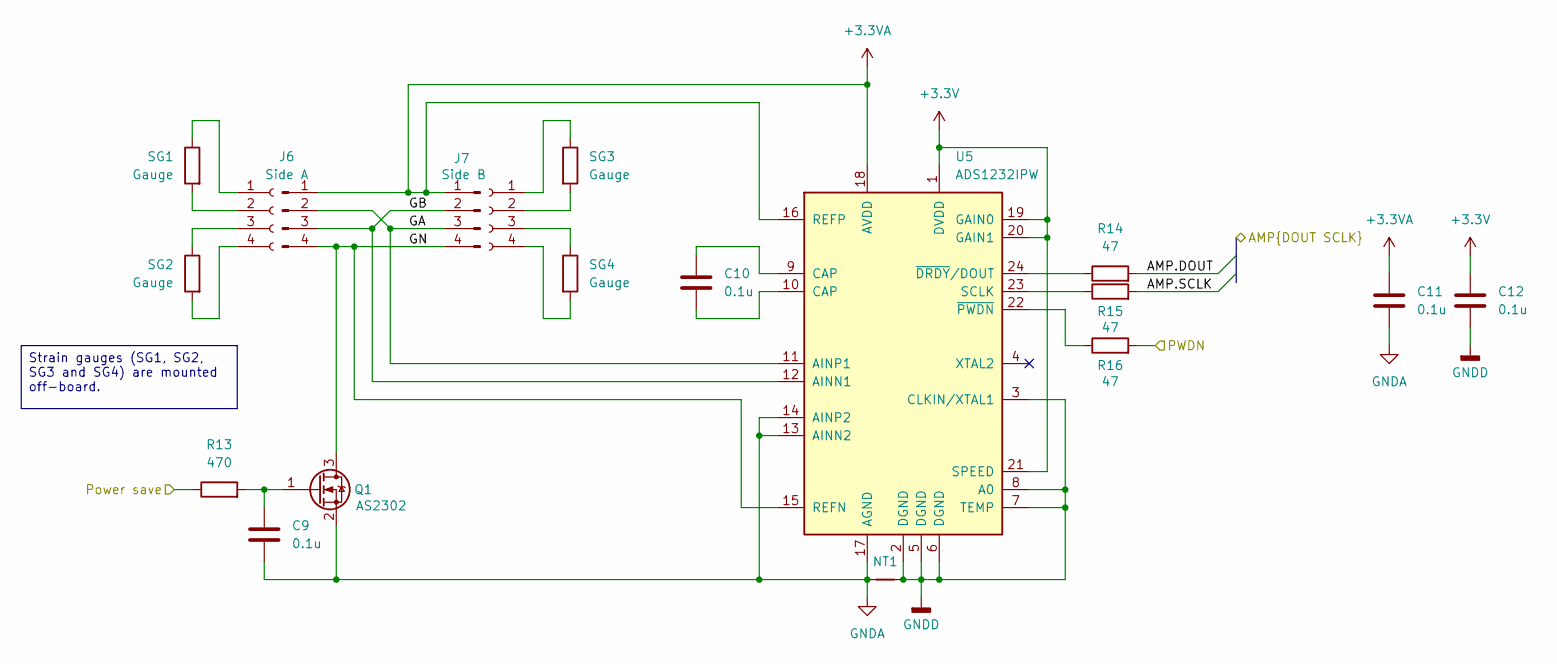
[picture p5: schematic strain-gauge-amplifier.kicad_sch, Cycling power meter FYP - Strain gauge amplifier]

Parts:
C9, C10, C11, C12: 0.1u; C_0603_1608Metric_Pad1.08x0.95mm_HandSolder
J6: Side A; PinHeader_1x04_P2.54mm_Vertical
J7: Side B; PinHeader_1x04_P2.54mm_Vertical
NT1: NetTie_2; NetTie-2_SMD_Pad0.5mm
Q1: AS2302; TSOT-23
R13: 470; R_0603_1608Metric_Pad0.98x0.95mm_HandSolder
R14, R15, R16: 47; R_0603_1608Metric_Pad0.98x0.95mm_HandSolder
SG1, SG2, SG3, SG4: Gauge
U5: ADS1232IPW; TSSOP-24_4.4x7.8mm_P0.65mm

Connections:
+3.3V: C12.1, U5.1 (DVDD), U5.19 (GAIN0), U5.20 (GAIN1), U5.21 (SPEED); also elsewhere on the board
+3.3VA: C11.1, J6.1, J7.1, U5.16 (REFP), U5.18 (AVDD); also elsewhere on the board
/AMP1.DOUT: R14.2; also elsewhere on the board
/AMP1.SCLK: R15.2; also elsewhere on the board
/AMP_PWDN: R16.2; also elsewhere on the board
/Power save: R13.1; also elsewhere on the board
/Strain gauge amplifier/GA: J6.2, J7.3, U5.11 (AINP1)
/Strain gauge amplifier/GB: J6.3, J7.2, U5.12 (AINN1)
/Strain gauge amplifier/GN: J6.4, J7.4, Q1.3 (D), U5.15 (REFN)
GNDA: C9.2, C11.2, NT1.1, Q1.2 (S), U5.13 (AINN2), U5.14 (AINP2), U5.17 (AGND); also elsewhere on the board
GNDD: C12.2, NT1.2, U5.2 (DGND), U5.3 (CLKIN/XTAL1), U5.5 (DGND), U5.6 (DGND), U5.7 (TEMP), U5.8 (A0); also elsewhere on the board
unnamed: C10.1, U5.9 (CAP)
unnamed: C10.2, U5.10 (CAP)
unnamed: C9.1, Q1.1 (G), R13.2
unnamed: SG1.1, SG1.2, SG2.1, SG2.2, SG3.1, SG3.2, SG4.1, SG4.2
unnamed: R15.1, U5.23 (SCLK)
unnamed: R14.1, U5.24 (~DRDY/DOUT)
unnamed: R16.1, U5.22 (~PWDN)

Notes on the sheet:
Strain gauges (SG1, SG2, SG3 and SG4) are mounted off-board.

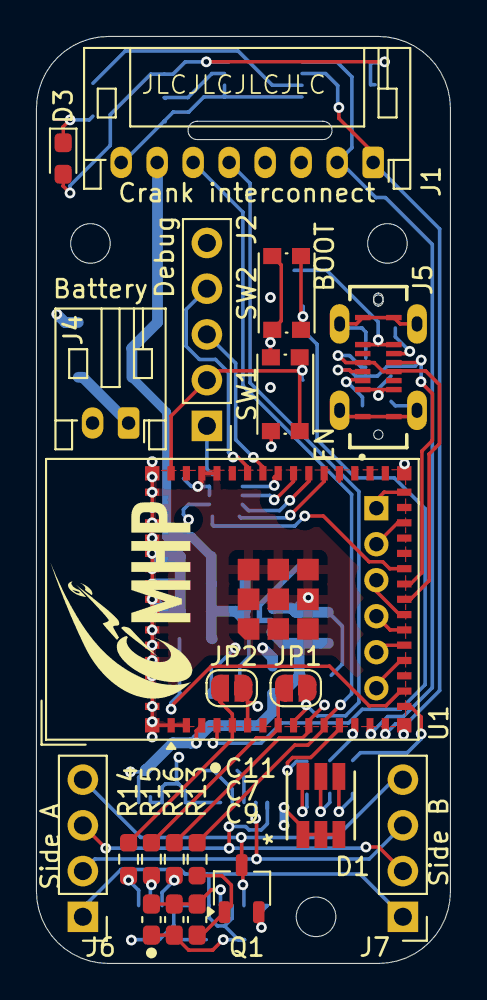
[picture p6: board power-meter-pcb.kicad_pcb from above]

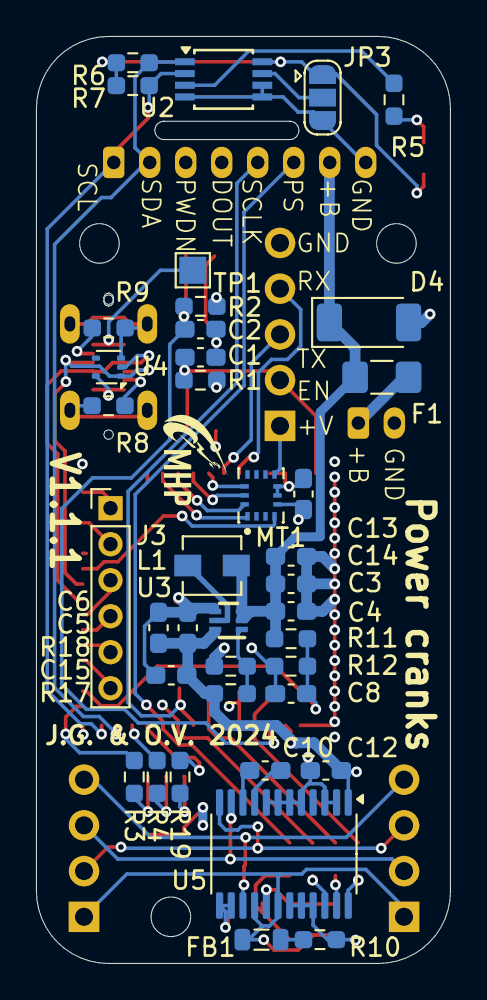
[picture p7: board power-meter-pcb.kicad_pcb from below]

Board: 4 copper layers, 23.0 x 51.5 mm, 64 parts (40 on the bottom side), 56 nets.

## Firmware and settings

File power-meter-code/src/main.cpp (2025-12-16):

/**
 * @file power-meter-code.ino
 * @brief Main file for a cycling power meter.
 *
 *
 * @author Jotham Gates and Oscar Varney, MHP
 * @version 0.1.0
 * @date 2024-10-01
 */
#include <Arduino.h>
#include "defines.h"
#include "src/power_meter.h"
#include "src/states.h"
#include "src/connections.h"
#include "src/connection_mqtt.h"
#include "src/connection_ble.h"
#include "src/config.h"
#include "src/lights.h"

SemaphoreHandle_t serialMutex;
TaskHandle_t imuTaskHandle, lowSpeedTaskHandle, connectionTaskHandle, ledTaskHandle, fancyLedTaskHandle;
portMUX_TYPE spinlock = portMUX_INITIALIZER_UNLOCKED;
Preferences prefs;

// Main states for the state machine.
extern StateSleep sleepState;
StateFlatBattery flatState;
StateActive activeState(sleepState, flatState);
StateSleep sleepState(activeState);

PowerMeter powerMeter;
Config config;

// Initialise the connection. We need a pointer to it's parent class that isn't on the stack to use as a task parameter.
MQTTConnection connectionMQTT;
BLEConnection connectionBLE;
Connection *connectionBasePtr;

void setup()
{
    pinMode(PIN_LEDR, OUTPUT);
    digitalWrite(PIN_LEDR, HIGH);
    // Initialise mutexes
    serialMutex = xSemaphoreCreateMutex(); // Needs to be created before logging anything.
    Serial.begin(SERIAL_BAUD); // Already running from the bootloader.
    Serial.setTimeout(30000);
    LOGI("Setup", "MHP Power meter " SW_VERSION ", " HW_VERSION_STR ". Compiled " __DATE__ ", " __TIME__);

    // Load config
    config.load();
    config.print();

    delay(50); // Help the temp sensors start?
    // LEDs (important to get the task started early).
    xTaskCreatePinnedToCore(
        taskLED,
        "LED",
        2048,
        NULL,
        1,
        &ledTaskHandle,
        1);
    delay(50); // Avoid race conditions and maybe help temp sensors start correctly?

    // Start the hardware.
    powerMeter.begin();
    
    pinMode(PIN_BOOT, INPUT);

    // Initialise the selected connection.
    switch (config.connectionMethod)
    {
    case CONNECTION_MQTT:
        // connectionMQTT.begin();
        connectionBasePtr = &connectionMQTT;
        break;
    case CONNECTION_BLE:
        // connectionBLE.begin();
        connectionBasePtr = &connectionBLE;
        break;
    }

    // xTaskCreatePinnedToCore(
    //     taskConnection,
    //     "Connection",
    //     9000,
    //     connectionBasePtr,
    //     1,
    //     &connectionTaskHandle,
    //     1);
    // TODO: Avoid race condition where the task handle is not initialised to enable or disable the connection.
    delay(100); // Very dodgy way to make sure the condition is avoided.

    // Start tasks
    // TODO: Determine RAM allocations

    // Communications need to have started before creating low speed. This also relies on queues created in power meter
    // Side::begin()
    xTaskCreatePinnedToCore(
        taskLowSpeed,
        "LowSpeed",
        4096,
        NULL,
        1, // Low priority.
        &lowSpeedTaskHandle,
        1);
    delay(100);

    // Low speed and communications need to have started before IMU.
    xTaskCreatePinnedToCore(
        taskIMU,
        "IMU",
        4096,
        NULL,
        3, // Make this a higher priority than other tasks.
        &imuTaskHandle,
        0); // Pin to core 0 so that we don't miss interrupts when updating the LEDs.
    delay(100);

    // Fancy Christmas lights task.
    xTaskCreatePinnedToCore(
        taskChristmasLeds,
        "Christmas",
        4096,
        NULL,
        2,
        &fancyLedTaskHandle,
        1);
    delay(100);

    // Create tasks to read data from ADCs
    // powerMeter.sides[SIDE_LEFT].createDataTask(SIDE_LEFT);
    // powerMeter.sides[SIDE_RIGHT].createDataTask(SIDE_RIGHT);
}

void loop()
{
    // Run the state machine
    runStateMachine("Main States", &activeState);
}

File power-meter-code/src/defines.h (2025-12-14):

/**
 * @file defines.h
 * @brief Useful pin and constant definitions and preprocessor directives.
 *
 *
 * @author Jotham Gates and Oscar Varney, MHP
 * @version 0.1.0
 * @date 2025-08-16
 */
#pragma once
#define SW_VERSION "s0.1.0"
#include "constants.h"

/**
 * Hardware versions
 */
// Check the versions are valid.
#if !defined(HW_VERSION)
#error "No hardware version specified (set this in constants.h)."
#endif
#if (HW_VERSION != HW_VERSION_V1_0_4) && (HW_VERSION != HW_VERSION_V1_0_5) && (HW_VERSION != HW_VERSION_V1_1_1)
#error "Unsupported hardware version specified (set this in constants.h)"
#endif

// Define a nicely formatted version string according to the version.
#if HW_VERSION == HW_VERSION_V1_0_4
#define HW_VERSION_STR "v1.0.4"
#elif HW_VERSION == HW_VERSION_V1_0_5
#define HW_VERSION_STR "v1.0.5"
#elif HW_VERSION == HW_VERSION_V1_1_1
#define HW_VERSION_STR "v1.1.1"
#endif

/**
 * Pins and hardware details
 */
// Strain gauge amplifiers
#define PIN_AMP1_DOUT 1
#define PIN_AMP1_SCLK 4
#define PIN_AMP2_DOUT 2
#define PIN_AMP2_SCLK 5
#define PIN_AMP_PWDN 6
#define PIN_POWER_SAVE 7
#define AMP_BIT_DEPTH 24

// Buttons and LEDs
#if (HW_VERSION == HW_VERSION_V1_0_4) || (HW_VERSION == HW_VERSION_V1_0_5)
#define PIN_LEDR 8
#define PIN_LEDG 9
// #define PIN_LEDB 12 // No Blue LED
#define PIN_CONNECTION_LED PIN_LEDG
#elif HW_VERSION == HW_VERSION_V1_1_1
#define PIN_LEDR 12
#define PIN_LEDG 9
#define PIN_LEDB 8
#define PIN_CONNECTION_LED PIN_LEDG
#define HAS_BLUE_LED
#endif

#define PIN_BOOT 0

// I2C for temperature sensor
#define PIN_I2C_SDA 10
#define PIN_I2C_SCL 11
#define I2C_BUS_FREQ 400000
#define TEMP1_I2C 0b1001001
#define TEMP2_I2C 0b1001000

// Accelerometer
#if (HW_VERSION == HW_VERSION_V1_0_4) || (HW_VERSION == HW_VERSION_V1_0_5)
#define PIN_ACCEL_INTERRUPT 38
#elif (HW_VERSION == HW_VERSION_V1_1_1)
#define ACCEL_RTC_CAPABLE
#define PIN_ACCEL_INTERRUPT 21
#endif
#define PIN_SPI_SDI 39
#define PIN_SPI_SDO 40
#define PIN_SPI_SCLK 41
#define PIN_SPI_AC_CS 42
#define IMU_SAMPLE_RATE 100 // Options are 12, 25, 50, 100, 200, 400, 800, 1600 Hz (any other value defaults to 100 Hz).
#define IMU_ACCEL_RANGE 4   // Options are 2, 4, 8, 16 G (any other value defaults to 16 G).
#define IMU_GYRO_RANGE 2000 // Options are 250, 500, 1000, 2000 dps (any other value defaults to 2000 dps).

// Power management
#if HW_VERSION == HW_VERSION_V1_0_4
#define PIN_BATTERY_VOLTAGE 12 // As per design.
#elif HW_VERSION == HW_VERSION_V1_0_5
#define PIN_BATTERY_VOLTAGE 15 // Bodge wire as original is shorted to ground.
#elif HW_VERSION == HW_VERSION_V1_1_1
#define PIN_BATTERY_VOLTAGE 13
#endif

// Extra GPIO pins
#if (HW_VERSION == HW_VERSION_V1_0_4) || (HW_VERSION == HW_VERSION_V1_0_5)
// Spare GPIO pins are // TODO:
#define SPARE_GPIO_6 15
#elif (HW_VERSION == HW_VERSION_V1_1_1)
#define SPARE_GPIO_1 48
#define SPARE_GPIO_2 33
#define SPARE_GPIO_3 18
#define SPARE_GPIO_4 17
#define SPARE_GPIO_5 16
#define SPARE_GPIO_6 15
#endif

#define PIN_LEDS 43

// Communications
#define PIN_UART_TX0
#define PIN_UART_RX0
#define SERIAL_BAUD 115200
#define PIN_USB_DN 19
#define PIN_USB_DP 20

/**
 * Logging
 * // TODO: Make work over USB.
 */
// Logging (with mutexes)
#define SERIAL_TAKE() xSemaphoreTake(serialMutex, portMAX_DELAY)
#define SERIAL_GIVE() xSemaphoreGive(serialMutex)
#define LOGV(tag, format, ...)                 \
    SERIAL_TAKE();                             \
    log_v("[%s] " format, tag, ##__VA_ARGS__); \
    SERIAL_GIVE()
#define LOGD(tag, format, ...)                 \
    SERIAL_TAKE();                             \
    log_d("[%s] " format, tag, ##__VA_ARGS__); \
    SERIAL_GIVE()
#define LOGI(tag, format, ...)                 \
    SERIAL_TAKE();                             \
    log_i("[%s] " format, tag, ##__VA_ARGS__); \
    SERIAL_GIVE()
#define LOGW(tag, format, ...)                 \
    SERIAL_TAKE();                             \
    log_w("[%s] " format, tag, ##__VA_ARGS__); \
    SERIAL_GIVE()
#define LOGE(tag, format, ...)                 \
    SERIAL_TAKE();                             \
    log_e("[%s] " format, tag, ##__VA_ARGS__); \
    SERIAL_GIVE()

// https://gcc.gnu.org/onlinedocs/gcc-4.8.5/cpp/Stringification.html
#define xstringify(s) stringify(s)
#define stringify(s) #s

/**
 * @brief Enumerator to represent each side of the power meter.
 *
 */
enum EnumSide
{
    SIDE_LEFT = 0,
    SIDE_RIGHT = 1,
    SIDE_IMU_TEMP = 2
};

/**
 * @brief Enumerator to represent the selected connection method.
 *
 */
enum EnumConnection
{
    CONNECTION_MQTT,
    CONNECTION_BLE
};

/**
 * @brief Enumerator for connection state
 *
 */
enum EnumConnState
{
    CONN_STATE_DISABLED,
    CONN_STATE_CONNECTING_1,
    CONN_STATE_CONNECTING_2,
    CONN_STATE_ACTIVE,
    CONN_STATE_SHUTTING_DOWN,
    CONN_STATE_SENDING,
    CONN_STATE_RECEIVING
};
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

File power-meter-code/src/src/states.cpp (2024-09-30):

/**
 * @file states.cpp
 * @brief Framework for the state machine.
 *
 * Loosly based on code from the burgler alarm extension of this project:
 * https://github.com/jgOhYeah/BikeHorn
 *
 *
 * @author Jotham Gates and Oscar Varney, MHP
 * @version 0.1.0
 * @date 2024-10-01
 */
#include "states.h"
extern SemaphoreHandle_t serialMutex;

// Don't include in the header file to stop circular issues.
#include "connections.h"
extern Connection *connectionBasePtr;
extern PowerMeter powerMeter;
extern Config config;

#include "soc/rtc_cntl_reg.h"

State *StateActive::enter()
{
    connectionBasePtr->enable();
    powerMeter.powerUp();

    // Main housekeeping loop
    while (m_isActive())
    {
        // Populate and send the housekeeping data. Update the temperatures at the same time.
        HousekeepingData housekeeping;
        housekeeping.temperatures[SIDE_LEFT] = powerMeter.sides[SIDE_LEFT].tempSensor.readTemp();
        housekeeping.temperatures[SIDE_RIGHT] = powerMeter.sides[SIDE_RIGHT].tempSensor.readTemp();
        housekeeping.temperatures[SIDE_IMU_TEMP] = powerMeter.imuManager.getLastTemperature();
        housekeeping.battery = powerMeter.batteryVoltage();
        housekeeping.offsets[SIDE_LEFT] = config.strain[SIDE_LEFT].offset;
        housekeeping.offsets[SIDE_RIGHT] = config.strain[SIDE_RIGHT].offset;
        connectionBasePtr->addHousekeeping(housekeeping);

        // Shut down if the battery is flat a certain number of times in a row.
        if (housekeeping.battery < MINIMUM_BATTERY)
        {
            // Flat this time.
            m_flatSuccessiveReadings--;
            if (!m_flatSuccessiveReadings)
            {
                // Flat several times in a row. Time to shut down.
                return &m_flatState;
            }
        }
        else
        {
            // Reset counter.
            m_flatSuccessiveReadings = MINIMUM_BATTERY_SUCCESSIVE;
        }

        debugMemory();

        // Delay for ~10s whilst checking UI regularly.
        for (int i = 0; i < 100; i++)
        { 
            // If the boot button is pressed, toggle the connection method on next boot.
            if (digitalRead(PIN_BOOT) == LOW)
            {
                // Boot button is pressed.
                LOGI("Housekeeping", "Boot button pressed. Will toggle connection mode.");
                config.toggleConnection();
                config.save();
                reboot(false);
            }

            // Check if we received anything on the serial port and if so, act on it.
            if (Serial && Serial.available())
            {
                char value = Serial.read();
                switch (value)
                {
                case 'r':
                case 'R':
                    // Reboot normally.
                    reboot(false);
                    break;

                case 'p':
                case 'P':
                    // Reboot into download mode.
                    reboot(true);
                    break;

                case 'g':
                case 'G':
                    // Gets the config and prints them.
                    config.print();
                    break;

                case 's':
                case 'S':
                    // Read configs from the serial port and update them.
                    config.serialRead();
                    break;

                case 'f':
                case 'F':
                    // Reset config to defaults.
                    config.removeKey();
                    LOGI("Housekeeping", "Config will be reset on next boot.");
                    break;
                
                case 'c':
                case 'C':
                    // Perform offset compensation.
                    powerMeter.offsetCompensate();
                    break;

                default:
                    // Unrecognised, print an unrecognised message and follow on to the help text.
                    LOGW("Housekeeping", "Unrecognised instruction '%c'.", value);
                case 'h':
                case 'H':
                    printHelp();
                }

                // Clear the buffer
                while (Serial.available())
                {
                    Serial.read();
                }
            }

            delay(100);
        }
    }
    return &m_sleepState;
}

bool StateActive::m_isActive()
{
    // Calculate how long it has been since the last rotation.
    LowSpeedData data;
    powerMeter.imuManager.setLowSpeedData(data);
    uint32_t duration = (micros() - data.timestamp) / 1000000L;

    // Work out if it has been too long.
    return config.sleepTime == 0 || duration < config.sleepTime;
}

State *StateSleep::enter()
{
    LOGD("Sleep", "Shutting down the hardware");
    connectionBasePtr->disable();
    powerMeter.leds.setImpendingSleep();
    powerMeter.imuManager.enableMotion();
    delay(2000);
    powerMeter.powerDown();
    LOGD("Sleep", "Going to sleep");
#ifdef ACCEL_RTC_CAPABLE
    esp_sleep_enable_ext0_wakeup((gpio_num_t)PIN_ACCEL_INTERRUPT, HIGH);
#else
    LOGE("Sleep", "This hardware version can't accept accelerometer interrupts in sleep mode!");
    esp_sleep_enable_timer_wakeup(20000000); // 20s to simulate
#endif

    // Start deep sleep. The MCU will restart on wake.
    esp_deep_sleep_start();
}

State *StateFlatBattery::enter()
{
    LOGD("Flat", "Shutting down the hardware");
    connectionBasePtr->disable();
    powerMeter.leds.setImpendingSleep();
    powerMeter.imuManager.enableMotion(); // TODO: Shutdown entirely.
    delay(2000);
    powerMeter.powerDown();
    LOGD("Flat", "Going to sleep permenantly");
    esp_sleep_disable_wakeup_source(ESP_SLEEP_WAKEUP_ALL);
    esp_deep_sleep_start();
}

void reboot(bool dfu)
{
    LOGW("Reboot", "About to reboot.");
    connectionBasePtr->disable();
    powerMeter.powerDown();
    if (dfu)
    {
        LOGW("Reboot", "Will reboot into DFU mode, reset to exit afterwards.");
        REG_WRITE(RTC_CNTL_OPTION1_REG, RTC_CNTL_FORCE_DOWNLOAD_BOOT);
    }

    // Allow plenty of time to shut everything down nicely. Flash the LEDs so it is a bit more obvious.
    for (uint8_t i = 0; i < 25; i++)
    {
        powerMeter.sides[SIDE_LEFT].tempSensor.setLED(true);
        powerMeter.sides[SIDE_LEFT].tempSensor.setLED(true);
        digitalWrite(PIN_LEDR, HIGH);
        digitalWrite(PIN_LEDG, HIGH);
        delay(100);
        powerMeter.sides[SIDE_LEFT].tempSensor.setLED(false);
        powerMeter.sides[SIDE_LEFT].tempSensor.setLED(false);
        digitalWrite(PIN_LEDR, LOW);
        digitalWrite(PIN_LEDG, LOW);
        delay(100);
    }

    // Enough warning, should be ok to reboot.
    esp_restart();
}
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

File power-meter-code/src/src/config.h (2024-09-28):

/**
 * @file config.h
 * @brief Classes that handles configuration.
 *
 * @author Jotham Gates and Oscar Varney, MHP
 * @version 0.1.0
 * @date 2024-09-28
 */
#pragma once
#include "../defines.h"
#include <BasicLinearAlgebra.h>
#include <Preferences.h>
#include <ArduinoJson.h>
using namespace BLA;

#define CONF_KEY "power-conf"
#define CONF_JSON_TEXT_LENGTH 1000

/**
 * @brief Class that bundles all the configs / calibration settings for a strain gauge.
 *
 */
class StrainConf
{
public:
    /**
     * @brief Writes the strain gauge config to a JsonObject.
     *
     * @param json is the object to write to.
     */
    void writeJSON(JsonObject json);

    /**
     * @brief Reads a JSON document into this object.
     *
     * @param doc The document to read data from.
     */
    void readJSON(JsonObject doc);

    uint32_t offset = DEFAULT_STRAIN_OFFSET;
    float coefficient = DEFAULT_STRAIN_COEFFICIENT;
    float tempTest = DEFAULT_STRAIN_TEST_TEMP;
    float tempCoefficient = DEFAULT_STRAIN_TEMP_CO;
};

#define CONF_WIFI_SSID_MAX_LENGTH 40   // Includes terminating null.
#define CONF_WIFI_PSK_MAX_LENGTH 64    // Includes terminating null.
#define CONF_MQTT_BROKER_MAX_LENGTH 64 // Includes terminating null.

/**
 * @brief Class that contains configs.
 *
 */
class Config
{
public:
    /**
     * @brief Loads data from flash memory.
     *
     */
    void load();

    /**
     * @brief Saves the preferences to flash memory.
     *
     */
    void save();

    /**
     * @brief Prints the current settings loaded into RAM.
     *
     */
    void print();

    /**
     * @brief Reads new config in from the serial terminal.
     *
     */
    void serialRead();

    /**
     * @brief Reads a string containing JSON data and extracts preferences from this.
     *
     * @param text the text containing the JSON data.
     * @param length the maximum length of the text.
     * @return true successfully read.
     * @return false failed to read.
     */
    bool readJSON(char *text, uint32_t length);

    /**
     * @brief Writes the config to JSON.
     *
     * @param text the text buffer to put the result in.
     * @param length the maximum length. Should be at least `CONF_JSON_TEXT_LENGTH`.
     */
    void writeJSON(char *text, uint32_t length, bool showWiFi = false);

    /**
     * @brief Writes the config to a JSON object.
     *
     * @param json is the object to write to.
     */
    void writeJSON(JsonVariant doc, bool showWiFi = false);

    /**
     * @brief Toggles the connection between WiFi / MQTT and BLE.
     *
     */
    void toggleConnection();

    /**
     * @brief Removes the config key from storage.
     *
     */
    void removeKey();

    EnumConnection connectionMethod = CONNECTION_MQTT;
    Matrix<2, 2, float> qEnvCovariance = DEFAULT_KALMAN_Q;
    Matrix<2, 2, float> rMeasCovariance = DEFAULT_KALMAN_R;
    int8_t imuHowOften = 1; // Set to -1 to disable sending IMU data.
    StrainConf strain[2];
    uint16_t mqttPacketSize = 50;
    char wifiSSID[CONF_WIFI_SSID_MAX_LENGTH] = DEFAULT_WIFI_SSID;
    char wifiPSK[CONF_WIFI_PSK_MAX_LENGTH] = DEFAULT_WIFI_PASSWORD;
    char mqttBroker[CONF_MQTT_BROKER_MAX_LENGTH] = DEFAULT_MQTT_BROKER;
    uint16_t sleepTime = DEFAULT_SLEEP_TIME;
    // TODO: device name, MQTT prefix.

private:
    /**
     * @brief Safely copies a string and makes sure that the last char is null.
     *
     * @param dest The destination to copy to.
     * @param source The source string.
     * @param maxLength The maximum length to copy.
     */
    void m_safeReadString(char *dest, const char *source, size_t maxLength);

    /**
     * @brief Writes a matrix to a json document.
     *
     * @param json JSON array to write to.
     * @param matrix Matrix to use values from.
     */
    void m_writeMatrix(JsonArray jsonArray, Matrix<2, 2, float> matrix);

    /**
     * @brief Reads a 2x2 matrix from a JSON array.
     *
     * @param jsonArray the matrix to read from.
     * @return Matrix<2, 2, float> the matrix.
     */
    Matrix<2, 2, float> m_readMatrix(JsonArray jsonArray);
};

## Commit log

2024-04-17 Created KiCAD project
    [power-meter-pcb.kicad_pcb, power-meter-pcb.kicad_sch]
2024-04-18 Added amplifier, IMU, inter board connections
    [accelerometer.kicad_sch, power-meter-pcb.kicad_pcb, power-meter-pcb.kicad_sch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]
2024-04-18 Assigning footprints, extremely rough idea of size
    [accelerometer.kicad_sch, power-meter-pcb.kicad_pcb, power-meter-pcb.kicad_sch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]
2024-04-20 Added power supply to PCB
    [accelerometer.kicad_sch, power-meter-pcb.kicad_pcb, power-meter-pcb.kicad_sch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]
2024-04-20 Started PCB layout
    [accelerometer.kicad_sch, power-meter-pcb.kicad_pcb, power-meter-pcb.kicad_sch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]
2024-04-22 Adding filtering and pullup resistors, board layout
    [power-meter-pcb.kicad_pcb, power-meter-pcb.kicad_sch, strain-gauge-amplifier.kicad_sch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]
2024-04-23 Routing and component placement continues
    [accelerometer.kicad_sch, power-meter-pcb.kicad_pcb, power-meter-pcb.kicad_sch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]
2024-04-23 Tidying schematic
    [accelerometer.kicad_sch, power-meter-pcb.kicad_sch, strain-gauge-amplifier.kicad_sch]
2024-05-01 Improved board outline, in the middle of layout changes
    [accelerometer.kicad_sch, power-meter-pcb.kicad_pcb, power-meter-pcb.kicad_sch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]
2024-05-02 Layout almost done, but will likely swap to a 4 layer PCB
    [accelerometer.kicad_sch, power-meter-pcb.kicad_pcb, power-meter-pcb.kicad_sch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]
2024-05-09 Board layout about done, front silkscreen ok
    [power-meter-pcb.kicad_pcb, usb-charging.kicad_sch]
2024-05-14 Cleaning up PCB back and title box
    [accelerometer.kicad_sch, power-meter-pcb.kicad_pcb, power-meter-pcb.kicad_sch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]
2024-05-24 Exporting BOM, added layer to board sheet
    [power-meter-pcb.kicad_pcb]
2024-06-14 Smaller PCB design started
    [accelerometer.kicad_sch, power-meter-pcb.kicad_pcb, power-meter-pcb.kicad_sch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]
2024-06-14 Smaller board layout planned
    [power-meter-pcb.kicad_pcb, power-meter-pcb.kicad_sch]
2024-06-16 More track routing
    [power-meter-pcb.kicad_pcb]
2024-06-21 Board mostly routed, schematic page layout cleaned up
    [power-meter-pcb.kicad_pcb, power-meter-pcb.kicad_sch, usb-charging.kicad_sch]
2024-06-23 Silkscreen done
    [accelerometer.kicad_sch, power-meter-pcb.kicad_pcb, power-meter-pcb.kicad_sch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]
2024-06-24 Added date updating script.
    [power-meter-pcb.kicad_pcb]
2024-06-25 Added doxygen file, updated versioning scripts, add pin definitions and states, updated readme
2024-06-28 Started strain gauge and temp sensors classes
    [power-meter-pcb.kicad_sch]
2024-07-03 Added Kalman filter and testing for it
2024-07-04 Started IMU manager to connect kalman filter
2024-07-05 Re-centred schematics, added header for spare GPIO pins, touched up logos
    [accelerometer.kicad_sch, power-meter-pcb.kicad_pcb, power-meter-pcb.kicad_sch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]
2024-07-09 Moved IMU class to its own file, kalman filter should be updated automatically
2024-07-11 Added LED driven by temp sensor, updated numbering
    [accelerometer.kicad_sch, power-meter-pcb.kicad_pcb, power-meter-pcb.kicad_sch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]
2024-07-12 Fixed LED3 wiring
    [power-meter-pcb.kicad_pcb]
2024-07-15 Cap on ADC DC pin moved to next to pin
    [accelerometer.kicad_sch, power-meter-pcb.kicad_pcb, power-meter-pcb.kicad_sch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]
2024-07-22 Compiles, state name pointer doesn't work
    [connection_mqtt.h, power-meter-code.ino, states.cpp]
2024-07-29 Compiles with ESP32 board version 2.011, needs features from board version 3+
2024-08-01 Sends regular MQTT messages with IMUData
2024-08-02 Added python IMU logger, fixed scaled units for IMU,modified IMUData to have some raw data.
    [imu.cpp]
2024-08-04 Edited connections base class to be single parent, fixed kalman spinslock
    [connection_mqtt.h, defines.h, imu.cpp]
2024-08-08 Reads temperature, flashes amber LED, corrected bus labelling error in schematic.
    [power-meter-pcb.kicad_sch]
2024-08-08 Fixing I2C track labelling. V1.1.0
    [accelerometer.kicad_sch, power-meter-pcb.kicad_pcb, power-meter-pcb.kicad_sch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]
2024-08-09 Fixed SPI pin labels
    [accelerometer.kicad_sch, power-meter-pcb.kicad_pcb, power-meter-pcb.kicad_sch]
2024-08-10 Kalman filter appears to work
2024-08-14 Started writing code to read from strai ngauges, moved temperatures to their own file (untested)
2024-08-16 Kalman filter works still, swapped to USB OTG, can enter DFU using software.
    [states.cpp]
2024-08-21 Added testing script for all LEDs and temperature sensors.
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2024-08-23 Low data rate messages sent, can swap between connections, issues with data rates possibly
    [config.cpp, config.h, connection_ble.h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]
2024-08-23 Removed logging for each MQTT message to fix performance, moved keeping track of interrupt timings to the isr. Not tested for the ADC ISR templates.
    [imu.cpp, power-meter-code.ino, power_meter.cpp]
2024-08-30 Python scripts to log and plot strain data saved.
    [strain-gauge-amplifier.kicad_sch]
2024-09-03 Torque and average power are calculated and handled, CLI improved, offset compensation enabled.
2024-09-04 Swapped to platform IO
    [config.cpp, config.h, connection_ble.h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]
2024-09-04 Sends all IMU data, runs out of RAM
2024-09-07 USB CLI works again, buffer size issues with IMU data fixed, memory usage logged
    [connection_mqtt.h, main.cpp, power_meter.cpp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]
2024-09-08 Uses a TPS61022 Voltage regulator - will change for easier soldering
    [power-meter-pcb.kicad_pcb, usb-charging.kicad_sch]
2024-09-08 New voltage regulator layout about done
    [power-meter-pcb.kicad_pcb, usb-charging.kicad_sch]
2024-09-09 Added buffer size to conf, flashes an LED on TX, logger saves power and fully converts housekeeping to csv
2024-09-09 PCB modifications about done
    [accelerometer.kicad_sch, power-meter-pcb.kicad_pcb, power-meter-pcb.kicad_sch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]
2024-09-10 Added slot for thermal isolation
    [power-meter-pcb.kicad_pcb]
2024-09-10 Sorting out parts to order and component changes
    [accelerometer.kicad_sch, power-meter-pcb.kicad_sch, strain-gauge-amplifier.kicad_sch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]
2024-09-10 Added 3D model for RGB LED
    [power-meter-pcb.kicad_pcb]
2024-09-10 Fixed USB data pin polarity in one orientation, added test point
    [power-meter-pcb.kicad_pcb, usb-charging.kicad_sch]
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2024-09-24 Plot strain gauges shows ADC raw and min and max
2024-09-26 Swapped calibration to Nm
2024-09-27 Added offsets to housekeeping, option to use provided torque in plot strain
2024-09-27 Power is no longer off by 1e6, slow data is correctly sent to csv and graph, help strings updated.
    [main.cpp, power_meter.cpp]
2024-09-27 Plots cadence and power over time, flipped left and right order over on strain graph for aesthetics
2024-09-28 Swapped to arduinojson to serialise configs, changed config format, added mqtt and wifi to conf, now uses platformio libraries instead of arduino library folder.
    [config.cpp, config.h, constants.example.h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]
2024-09-30 Added MQTT topics page, added flat battery shutdown,
2024-10-02 Added FIT file support to plotter, time offsets, plotting individual left and right power, corrected power balance flipped.
    [power_meter.cpp]
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2024-10-04 Added temperature plot, strain and imu now correct for device time being reset.
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2024-10-11 Removed unnecessary call to turn off red LED, simplified calibration graphs
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2024-10-17 Added ability to export power comparisons to CSV
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2025-01-31 Started recalculating script, fixed power reporting for BLE
    [accelerometer.kicad_sch, power-meter-pcb.kicad_sch, strain-gauge-amplifier.kicad_sch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]
2025-08-16 Updated to KiCAD 9.0, copied parameters into constants.example.h, doubled reported battery voltage to suit latest boards with voltage divider fitted.
    [accelerometer.kicad_sch, power-meter-pcb.kicad_pcb, power-meter-pcb.kicad_sch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]
